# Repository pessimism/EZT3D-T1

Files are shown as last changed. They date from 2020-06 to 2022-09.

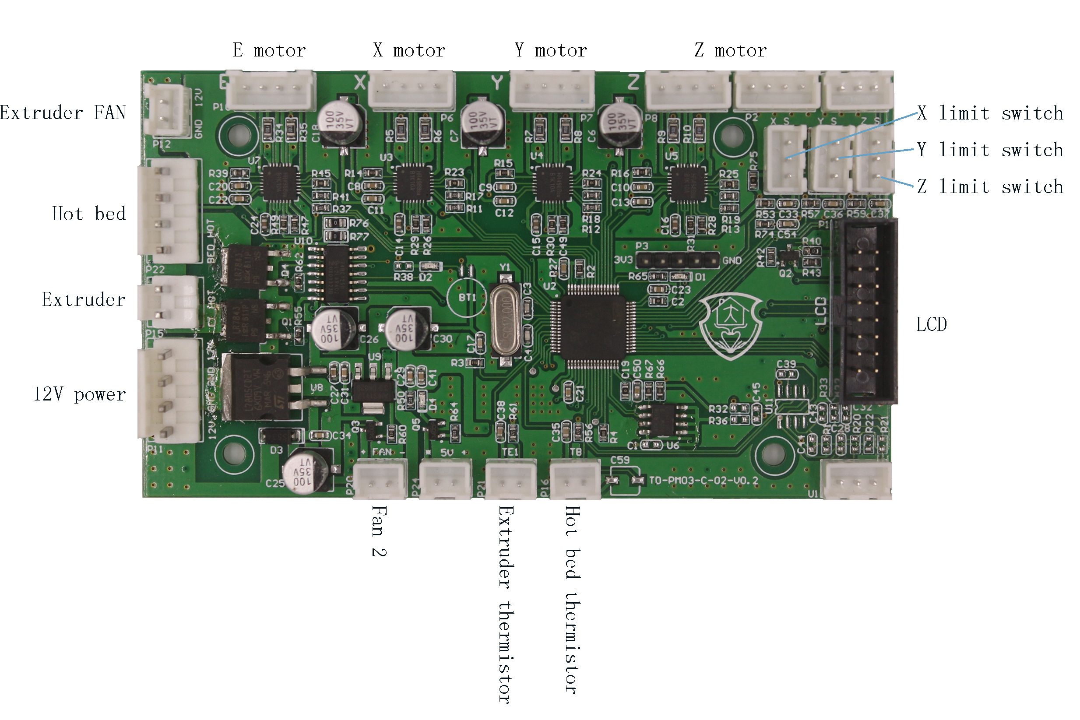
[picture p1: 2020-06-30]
FromSDCard/1.Installation Video/Main control board wiring scheme .jpg

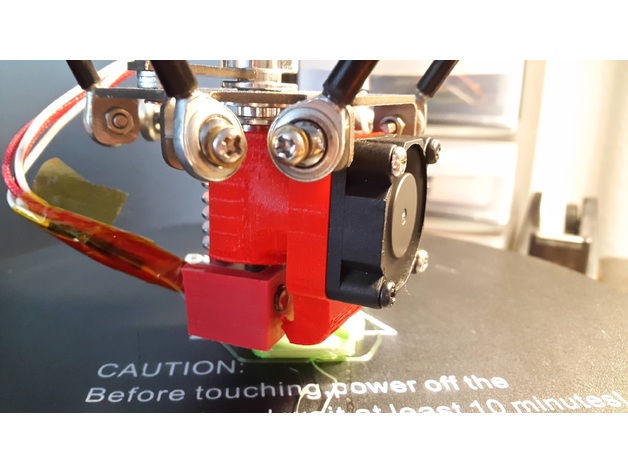
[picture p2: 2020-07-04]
Upgrade Part Models/E3Dv5+Hotend+30mm+Dual+Part+Cooling+Fan+Duct+fits+EZT+T1/images/20200701_104203.jpg

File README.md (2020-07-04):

# EZT3D-T1 3D Printer

I purchased this printer at [AliExpress](https://www.aliexpress.com/item/4001137583437.html) for $140.  I enjoy purchasing the least expensive printer kits I can find and seeing how far I can tweak them to produce good results.  The unit I received is a "T1-B1" model which is slightly different from the one picture in the installation video.

+ My other printer is a heavily modified Tronxy X1 which can now beat a Prusa i3 MK3 on the [AutoDesk FDM benchmark](https://github.com/kickstarter/kickstarter-autodesk-3d) at less than 25% of the cost.  The difference being that the Prusa is an all-day workhorse and the Tronxy requires constant tuning and tweaking to stay in calibration.

## Pre-Assembly Notes

+ The unit I purchased was an Australian 220V model.  I was able to use this in Canada on 110V with no issues by swapping out the line cord.  The power supply is unbranded and has no labelling or voltage selector, but there is what appears to be an active PFC IC inside on the board which indicates that it is voltage auto-sensing.  There was a sticker inside the box also that stated "110-220VAC".  

+ Regardless of where you are located, before building the printer, it is important to check for loose screws in the package.  A couple of the hardware bags had split and there was a loose metal T-Nut INSIDE the power supply.  Had I not caught that the magic smoke would have been released in short order.

+ Connect power to the power supply.  A green LED should light up.  Test the output voltage.  It should be very close to 12V (mine was 12.3).  There will be a lot of wiring around the power supply when done so it is best to check the power supply before building the printer.

+ If you want the flattest bed possible without purchasing glass, tape sheets of sandpaper (I had 120 and 220 grit, so I used those) to a piece of flat material (particle board shelving or countertops are manufactured straight and good for this).  Write a grid on the aluminum side of the bed in permanent marker to see where you have flattened.  Sand the aluminum across the sheets of sandpaper on your flat surface until the marker is gone.  It will be obvious which areas have been smoothed down and which aren't yet.  Mine was significantly concave and took a good 30-45 minutes of hard work to smooth out.  Credit to [this reddit thread](https://www.reddit.com/r/3Dprinting/comments/9fu812/sanding_my_warped_ender_3_bed_to_an_accuracy_of) for the idea!

+ The included carbon delta rods are of very poor quality.  They should be 200MM exactly from hole center to hole center.  The fisheyes screw into the hollow rods.  The rods in my kit did not have all of the fisheyes screwed in evenly so not only were they different lengths, they were all short of 200MM.  This causes a delta printer to have weird geometry problems.  In my case, there were areas of the bed where the print head would not get close enough to the bed to do a first layer.  In addition, two of the rod ends split when the fisheyes were tightened.  I put two zip ties over each split end to close them up and reinforce them and will be adding superglue for additional strength and to keep the fisheyes from rotating.

+ When assembling, make sure the ends of the aluminum extrusions are flush with the acrylic surfaces as per the installation video.  Once belts are installed they are under tension and the belts need to be removed to readjust their positioning.

+ The printer has no part cooling fan but has a header on the board for one.  If you have available wire/connectors, add a part cooling fan power lead to the wiring bundle as you are building the printer to avoid a lot of disassembly and wire movement to add one later

+ Out of the box the hotend puts a lot of heat into parts (moreso than other printers I've worked with) and prints very poorly.  In the "Upgrade Part Models" folder of this repository is a [copy of a duct from a thingiverse user](https://www.thingiverse.com/thing:4513844).  This redirects a small amount of the air from the hotend fan to act as part cooling and tremendously improves print quality as a stopgap until a proper part cooling fan can be installed.  If you have access to another printer, print and install this part as you build the printer.  If not, try to print this as soon as possible using the lowest temperature your filament can tolerate, heated bed at room temperature, and very low speeds.

+ The main board has the USB connector facing downward underneath the printer.  I recommend connecting the board to USB before building the printer, making sure it lights up and responds to an M503 command.  After the printer is built you will need either a right angle USB A adapter or feet to raise the printer enough to allow a cable to plug in and bend.  There is a model for feet in this repository.

## Control Board

+ The control board for the printer is an unbranded board with no visible part number. 

+ It uses an [STM32F103C8 CPU](https://www.st.com/resource/en/datasheet/stm32f103c8.pdf)

+ The stepper drivers are under heatsinks and I am assuming they are A4988 or similar.  XYZ are running 80 steps/MM.

+ The board seems to be running a very cut down, modified version of Marlin 1.0.  It does not respond to many common GCODE commands.  It uses a very small display and has a very limited menu system with no ability to adjust parameters other than temperature and print speed.  Features such as linear advance or mesh bed levelling are unavailable.  This severely limits the print quality that will be acheivable.

+ Marlin support for STM32 boards appears to be a mixed bag and given that, no documentation for the board and the unusual display used leaves little hope for an upgrade to Marlin 2.0.

## Extruder

+ The extruder is a plastic bodied unit with a single drive gear and an idler wheel.  Tension is not adjustable other than replacing the spring.  It appears to be a limiting factor in print speeds so far, with the motion system and hotend supporting more speed than it can keep up with.

## Hotend

+ The hotend is a low cost all-metal E3D V5 clone.  

+ It does not have a PTFE liner so should be suitable for materials such as PETG that require >240C temperatures.  

+ My unit has a poor fit between the heat break and heater block and requires frequent tightening to avoid filament seepage.  

+ The filament is hard to push through the transition between the upper heatsink and the heat break.  This does not help the already anemic extruder.  

+ The heater cartridge is slightly smaller in diameter than the bore in the heatblock.  I have seen this on other low cost-clones.  The heater cartridge can be shimmed with a couple of wraps of aluminum foil to acheive a tighter fit to the heat block and improve heat transfer.

## Frame

+ The acrylic frame is attached to the metal extrusions with only a few screws each.  There is significant flex and wobble.  There is a lot of potential for stiffener parts to be added to increase rigidity.

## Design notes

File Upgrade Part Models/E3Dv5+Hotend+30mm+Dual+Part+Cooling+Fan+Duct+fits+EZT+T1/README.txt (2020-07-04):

E3Dv5 Hotend 30mm Dual Part Cooling Fan Duct fits EZT T1 by Knutwurst on Thingiverse: https://www.thingiverse.com/thing:4513844

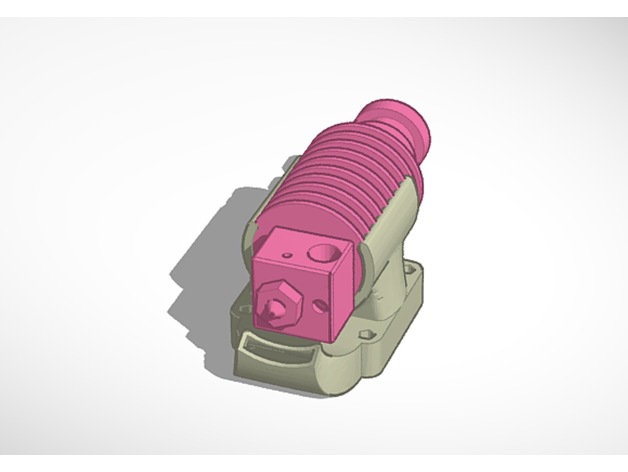
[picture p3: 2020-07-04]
Upgrade Part Models/E3Dv5+Hotend+30mm+Dual+Part+Cooling+Fan+Duct+fits+EZT+T1/images/Bildschirmfoto_2020-07-01_um_10.54.08.jpg

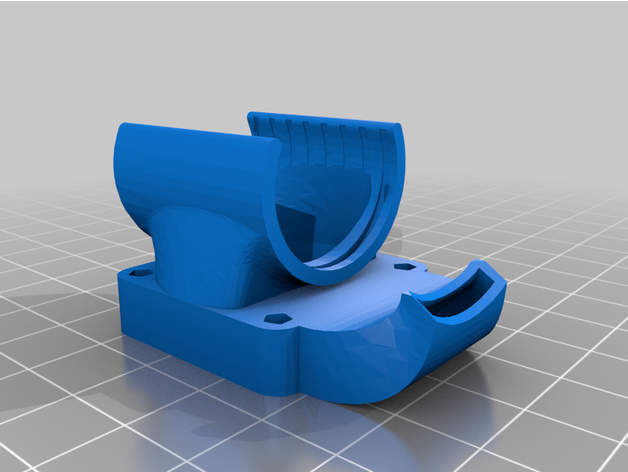
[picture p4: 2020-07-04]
Upgrade Part Models/E3Dv5+Hotend+30mm+Dual+Part+Cooling+Fan+Duct+fits+EZT+T1/images/T1_Cooler_V3.png

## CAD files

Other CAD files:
Calibration Models/Bed Check v2.stl
FromSDCard/5.model/liaojia.STL
Upgrade Part Models/4010 Part Cooler Mount for Effector/4010 Part Cooler Mount for Effector v7.stl
Upgrade Part Models/4010 Wind Mouth/4010 Wind Mouth v3.stl
Upgrade Part Models/E3Dv5+Hotend+30mm+Dual+Part+Cooling+Fan+Duct+fits+EZT+T1/files/T1_Cooler_V3.stl
Upgrade Part Models/Effector/Part Cooler Fan Holder.stl
Upgrade Part Models/EZT_T1_stand/files/Delta_fot.stl
Upgrade Part Models/MKS SGEN L 1.0 Adapter Plate/MKS SGEN L 1.0 Adapter Plate v22.stl
Upgrade Part Models/Renfort_montant_EZT3D_-_T1/files/RenfortBaseV2.stl
Upgrade Part Models/Upper Support/Upper Support v6.stl
Upgrade Part Models/Effector/Part1.stl
Upgrade Part Models/EZT_T1_stand/files/Delta_fot_V2.stl
Upgrade Part Models/MKS SGEN L 1.0 Adapter Plate/Front Half.stl
FromSDCard/5.model/reg30.STL
Upgrade Part Models/Effector/Part2.stl
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

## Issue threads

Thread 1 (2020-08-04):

Create .Bin file

defilippi82, 2020-08-04:
hello, my EZT T1 original board burned and I had to buy another one by Aliexpress, but it came with another firmware that the 3d printer 2.1 did not work I had Sinis 1.1, I got a .bin file with Marlin 2.0 but I don't know how to configure the bed which has a convex shape and the height of Z, it doesn't save in the EPEROOM, could you help me with that?

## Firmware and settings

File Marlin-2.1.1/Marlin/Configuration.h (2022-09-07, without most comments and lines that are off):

#pragma once
#define CONFIGURATION_H_VERSION 02010100
#define STRING_CONFIG_H_AUTHOR "Steve Trotman" // Who made the changes.
#define SHOW_BOOTSCREEN
  #define MOTHERBOARD BOARD_MKS_SGEN_L
#define SERIAL_PORT -1
#define BAUDRATE 250000
#define CUSTOM_MACHINE_NAME "EZT3D-T1-B1-S"
#define X_DRIVER_TYPE  TMC2208_STANDALONE
#define Y_DRIVER_TYPE  TMC2208_STANDALONE
#define Z_DRIVER_TYPE  TMC2208_STANDALONE
#define E0_DRIVER_TYPE A4988
#ifdef I_DRIVER_TYPE
  #define AXIS4_NAME 'A' // :['A', 'B', 'C', 'U', 'V', 'W']
  #define AXIS4_ROTATES
#endif
#ifdef J_DRIVER_TYPE
  #define AXIS5_NAME 'B' // :['B', 'C', 'U', 'V', 'W']
  #define AXIS5_ROTATES
#endif
#ifdef K_DRIVER_TYPE
  #define AXIS6_NAME 'C' // :['C', 'U', 'V', 'W']
  #define AXIS6_ROTATES
#endif
#ifdef U_DRIVER_TYPE
  #define AXIS7_NAME 'U' // :['U', 'V', 'W']
#endif
#ifdef V_DRIVER_TYPE
  #define AXIS8_NAME 'V' // :['V', 'W']
#endif
#ifdef W_DRIVER_TYPE
  #define AXIS9_NAME 'W' // :['W']
#endif
#define EXTRUDERS 1
#define DEFAULT_NOMINAL_FILAMENT_DIA 1.75
#define TEMP_SENSOR_0 11
#define TEMP_SENSOR_1 0
#define TEMP_SENSOR_2 0
#define TEMP_SENSOR_3 0
#define TEMP_SENSOR_4 0
#define TEMP_SENSOR_5 0
#define TEMP_SENSOR_6 0
#define TEMP_SENSOR_7 0
#define TEMP_SENSOR_BED 1
#define TEMP_SENSOR_PROBE 0
#define TEMP_SENSOR_CHAMBER 0
#define TEMP_SENSOR_COOLER 0
#define TEMP_SENSOR_BOARD 0
#define TEMP_SENSOR_REDUNDANT 0
#define DUMMY_THERMISTOR_998_VALUE  25
#define DUMMY_THERMISTOR_999_VALUE 100
#if TEMP_SENSOR_IS_MAX_TC(0)
  #define MAX31865_SENSOR_OHMS_0      100 // (Ω) Typically 100 or 1000 (PT100 or PT1000)
  #define MAX31865_CALIBRATION_OHMS_0 430 // (Ω) Typically 430 for Adafruit PT100; 4300 for Adafruit PT1000
#endif
#if TEMP_SENSOR_IS_MAX_TC(1)
  #define MAX31865_SENSOR_OHMS_1      100
  #define MAX31865_CALIBRATION_OHMS_1 430
#endif
#if HAS_E_TEMP_SENSOR
  #define TEMP_RESIDENCY_TIME         10  // (seconds) Time to wait for hotend to "settle" in M109
  #define TEMP_WINDOW                  1  // (°C) Temperature proximity for the "temperature reached" timer
  #define TEMP_HYSTERESIS              3  // (°C) Temperature proximity considered "close enough" to the target
#endif
#if TEMP_SENSOR_BED
  #define TEMP_BED_RESIDENCY_TIME      0  // (seconds) Time to wait for bed to "settle" in M190
  #define TEMP_BED_WINDOW              1  // (°C) Temperature proximity for the "temperature reached" timer
  #define TEMP_BED_HYSTERESIS          3  // (°C) Temperature proximity considered "close enough" to the target
#endif
#if TEMP_SENSOR_CHAMBER
  #define TEMP_CHAMBER_RESIDENCY_TIME 10  // (seconds) Time to wait for chamber to "settle" in M191
  #define TEMP_CHAMBER_WINDOW          1  // (°C) Temperature proximity for the "temperature reached" timer
  #define TEMP_CHAMBER_HYSTERESIS      3  // (°C) Temperature proximity considered "close enough" to the target
#endif
#if TEMP_SENSOR_REDUNDANT
  #define TEMP_SENSOR_REDUNDANT_SOURCE    E1  // The sensor that will provide the redundant reading.
  #define TEMP_SENSOR_REDUNDANT_TARGET    E0  // The sensor that we are providing a redundant reading for.
  #define TEMP_SENSOR_REDUNDANT_MAX_DIFF  10  // (°C) Temperature difference that will trigger a print abort.
#endif
#define HEATER_0_MINTEMP   5
#define HEATER_1_MINTEMP   5
#define HEATER_2_MINTEMP   5
#define HEATER_3_MINTEMP   5
#define HEATER_4_MINTEMP   5
#define HEATER_5_MINTEMP   5
#define HEATER_6_MINTEMP   5
#define HEATER_7_MINTEMP   5
#define BED_MINTEMP        5
#define CHAMBER_MINTEMP    5
#define HEATER_0_MAXTEMP 275
#define HEATER_1_MAXTEMP 275
#define HEATER_2_MAXTEMP 275
#define HEATER_3_MAXTEMP 275
#define HEATER_4_MAXTEMP 275
#define HEATER_5_MAXTEMP 275
#define HEATER_6_MAXTEMP 275
#define HEATER_7_MAXTEMP 275
#define BED_MAXTEMP      80
#define CHAMBER_MAXTEMP  60
#define HOTEND_OVERSHOOT 15   // (°C) Forbid temperatures over MAXTEMP - OVERSHOOT
#define BED_OVERSHOOT    10   // (°C) Forbid temperatures over MAXTEMP - OVERSHOOT
#define COOLER_OVERSHOOT  2   // (°C) Forbid temperatures closer than OVERSHOOT
#define PIDTEMP          // See the PID Tuning Guide at https://reprap.org/wiki/PID_Tuning
#define BANG_MAX 255     // Limits current to nozzle while in bang-bang mode; 255=full current
#define PID_MAX BANG_MAX // Limits current to nozzle while PID is active (see PID_FUNCTIONAL_RANGE below); 255=full current
#define PID_K1 0.95      // Smoothing factor within any PID loop
  #define DEFAULT_Kp 9.9
  #define DEFAULT_Ki 0.6
  #define DEFAULT_Kd 47
#define PIDTEMPBED
#define MAX_BED_POWER 255 // limits duty cycle to bed; 255=full current
  #define DEFAULT_bedKp 186.9
  #define DEFAULT_bedKi 34.45
  #define DEFAULT_bedKd 676.1
#define MAX_CHAMBER_POWER 255 // limits duty cycle to chamber heater; 255=full current
  #define PID_FUNCTIONAL_RANGE 10 // If the temperature difference between the target temperature and the actual temperature
  #define PID_EDIT_MENU         // Add PID editing to the "Advanced Settings" menu. (~700 bytes of flash)
  #define PID_AUTOTUNE_MENU     // Add PID auto-tuning to the "Advanced Settings" menu. (~250 bytes of flash)
#define PREVENT_COLD_EXTRUSION
#define EXTRUDE_MINTEMP 170
#define PREVENT_LENGTHY_EXTRUDE
#define EXTRUDE_MAXLENGTH 200
#define THERMAL_PROTECTION_HOTENDS // Enable thermal protection for all extruders
#define THERMAL_PROTECTION_BED     // Enable thermal protection for the heated bed
#define THERMAL_PROTECTION_CHAMBER // Enable thermal protection for the heated chamber
#define THERMAL_PROTECTION_COOLER  // Enable thermal protection for the laser cooling
#define DELTA
  #define DELTA_SEGMENTS_PER_SECOND 200
  #define DELTA_CALIBRATION_MENU
  #define DELTA_AUTO_CALIBRATION
    #define DELTA_CALIBRATION_DEFAULT_POINTS 4
    #define PROBE_MANUALLY_STEP 0.05      // (mm)
  #define DELTA_PRINTABLE_RADIUS 90.0    // (mm)
  #define DELTA_MAX_RADIUS       90.0    // (mm)
  #define DELTA_DIAGONAL_ROD 200.0        // (mm)
  #define DELTA_HEIGHT 322.84             // (mm) Get this value from G33 auto calibrate
  #define DELTA_ENDSTOP_ADJ { 0.0, -0.593, -0.650 } // Get these values from G33 auto calibrate
  #define DELTA_RADIUS 103.31              // (mm) Get this value from G33 auto calibrate
  #define DELTA_TOWER_ANGLE_TRIM { 0.168, -0.258, 0.089 } // Get these values from G33 auto calibrate
#define USE_XMAX_PLUG
#define USE_YMAX_PLUG
#define USE_ZMAX_PLUG
#define ENDSTOPPULLUPS
#define X_MIN_ENDSTOP_INVERTING true  // Set to true to invert the logic of the endstop.
#define Y_MIN_ENDSTOP_INVERTING true  // Set to true to invert the logic of the endstop.
#define Z_MIN_ENDSTOP_INVERTING true  // Set to true to invert the logic of the endstop.
#define I_MIN_ENDSTOP_INVERTING false // Set to true to invert the logic of the endstop.
#define J_MIN_ENDSTOP_INVERTING false // Set to true to invert the logic of the endstop.
#define K_MIN_ENDSTOP_INVERTING false // Set to true to invert the logic of the endstop.
#define U_MIN_ENDSTOP_INVERTING false // Set to true to invert the logic of the endstop.
#define V_MIN_ENDSTOP_INVERTING false // Set to true to invert the logic of the endstop.
#define W_MIN_ENDSTOP_INVERTING false // Set to true to invert the logic of the endstop.
#define X_MAX_ENDSTOP_INVERTING false  // Set to true to invert the logic of the endstop.
#define Y_MAX_ENDSTOP_INVERTING false  // Set to true to invert the logic of the endstop.
#define Z_MAX_ENDSTOP_INVERTING false  // Set to true to invert the logic of the endstop.
#define I_MAX_ENDSTOP_INVERTING false // Set to true to invert the logic of the endstop.
#define J_MAX_ENDSTOP_INVERTING false // Set to true to invert the logic of the endstop.
#define K_MAX_ENDSTOP_INVERTING false // Set to true to invert the logic of the endstop.
#define U_MAX_ENDSTOP_INVERTING false // Set to true to invert the logic of the endstop.
#define V_MAX_ENDSTOP_INVERTING false // Set to true to invert the logic of the endstop.
#define W_MAX_ENDSTOP_INVERTING false // Set to true to invert the logic of the endstop.
#define Z_MIN_PROBE_ENDSTOP_INVERTING true  // Set to true to invert the logic of the probe.
#define DETECT_BROKEN_ENDSTOP
#define XYZ_FULL_STEPS_PER_ROTATION 200
#define XYZ_MICROSTEPS 16
#define XYZ_BELT_PITCH 2
#define XYZ_PULLEY_TEETH 20
#define EXTRUDER_STEPS_PER_UNIT 142 //142 for dual gear extruder at 1/16 microstepping
#define DEFAULT_XYZ_STEPS_PER_UNIT ((XYZ_FULL_STEPS_PER_ROTATION) * (XYZ_MICROSTEPS) / double(XYZ_BELT_PITCH) / double(XYZ_PULLEY_TEETH))
#define DEFAULT_AXIS_STEPS_PER_UNIT   { DEFAULT_XYZ_STEPS_PER_UNIT, DEFAULT_XYZ_STEPS_PER_UNIT, DEFAULT_XYZ_STEPS_PER_UNIT, EXTRUDER_STEPS_PER_UNIT }  // default steps per unit for Kossel (GT2, 20 tooth)
#define DEFAULT_MAX_FEEDRATE          { 20000, 20000, 20000, 20000 }
#define DEFAULT_MAX_ACCELERATION      { 20000, 20000, 20000, 20000 }
#define DEFAULT_ACCELERATION          3000  // X, Y, Z ... and E acceleration for printing moves
#define DEFAULT_RETRACT_ACCELERATION  3000  // E acceleration for retracts
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

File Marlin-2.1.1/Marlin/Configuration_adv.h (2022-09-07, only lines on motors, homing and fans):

#define E0_AUTO_FAN_PIN -1
#define E1_AUTO_FAN_PIN -1
#define E2_AUTO_FAN_PIN -1
#define E3_AUTO_FAN_PIN -1
#define E4_AUTO_FAN_PIN -1
#define E5_AUTO_FAN_PIN -1
#define E6_AUTO_FAN_PIN -1
#define E7_AUTO_FAN_PIN -1
#define CHAMBER_AUTO_FAN_PIN -1
#define COOLER_AUTO_FAN_PIN -1
#define HOMING_BUMP_MM      { 5, 5, 5 }       // (linear=mm, rotational=°) Backoff from endstops after first bump
#define HOMING_BUMP_DIVISOR { 10, 10, 10 }    // Re-Bump Speed Divisor (Divides the Homing Feedrate)
#define MICROSTEP_MODES { 16, 16, 16, 16, 16, 16 } // [1,2,4,8,16]
#define LIN_ADVANCE
  #define LIN_ADVANCE_K 0.45    // Unit: mm compression per 1mm/s extruder speed

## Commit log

2020-06-30 Add files originally shipped with the printer
    [User Library-Quarer20_Nut.STL, liaojia.STL, ofw_face_front.STL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]
2020-07-04 add parts and initial profile
    [Bed Check v2.f3d, Bed Check v2.stl, Delta_fot.stl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]
2020-07-09 Add Marlin 2.0
    [Configuration.h, Configuration_adv.h]
2020-07-09 import default delta config
    [Configuration.h, Configuration_adv.h]
2020-07-09 add sample configs
    [Configuration.h, Configuration_adv.h]
2020-07-10 WIP marlin config for mks sgen l
    [Configuration.h]
2020-07-11 update config
    [Configuration.h, Configuration_adv.h]
2020-07-11 update with autocalibrate values
    [Configuration.h]
2020-08-16 update for tmc2208
    [Configuration.h]
2020-08-16 model updates
    [4010 Part Cooler Mount for Effector v7.stl, 4010 Wind Mouth v3.stl, Front Half.stl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]
2022-09-07 add marlin 2.1.1
    [Configuration.h, Configuration_adv.h, esp32.csv]
2022-09-07 start with generic delta config
    [Configuration.h, Configuration_adv.h]
2022-09-07 port config
    [Configuration.h]
2022-09-07 update to 2.1.1 instead of 2.1, doh!
    [Configuration.h, Configuration_adv.h]
2022-09-07 fresh hotend autotune
    [Configuration.h]
2022-09-07 fresh bed pid tune and delta calibration
    [Configuration.h]
2022-09-07 disable zigzag throttling
    [Configuration_adv.h]
2022-09-07 remove old marlin
    [Configuration.h, Configuration_adv.h]

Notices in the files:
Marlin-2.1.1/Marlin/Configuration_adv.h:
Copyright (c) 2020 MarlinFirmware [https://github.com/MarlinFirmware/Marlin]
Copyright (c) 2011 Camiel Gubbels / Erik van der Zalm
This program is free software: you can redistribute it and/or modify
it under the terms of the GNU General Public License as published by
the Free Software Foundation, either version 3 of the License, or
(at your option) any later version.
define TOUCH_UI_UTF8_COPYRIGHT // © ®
